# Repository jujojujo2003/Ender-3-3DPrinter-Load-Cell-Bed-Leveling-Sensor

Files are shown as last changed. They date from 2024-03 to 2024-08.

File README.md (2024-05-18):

# Ender-3-3DPrinter-Load-Cell-Bed-Leveling-Sensor
 This is a Load Cell based bed leveling sensor that should mount onto any vertical MGN12H gantry
 It uses
 * [ADS1235 ADC](https://www.digikey.com/en/products/detail/texas-instruments/ADS1235QWRHMRQ1/11308865) due to its 24-bit ADC, 7.2k sampling rate, 128x PGA gain.
 * [RP2040 MCU](https://www.raspberrypi.com/products/rp2040/) to do all the processing
 * [500g TAL 221 Loadcell](https://cdn.sparkfun.com/assets/9/9/a/f/3/TAL221.pdf) due to its compact nature. My gantry weighs around 250g. So make sure to select appropriate loadcell based on your gantry's weight so as to not saturate the loadcell.

My 3d printer is an Ender-3 with [3dFused's linear rail kit](https://3dfused.com/product/xaxis235/) and it perfectly works with that.

## PCB
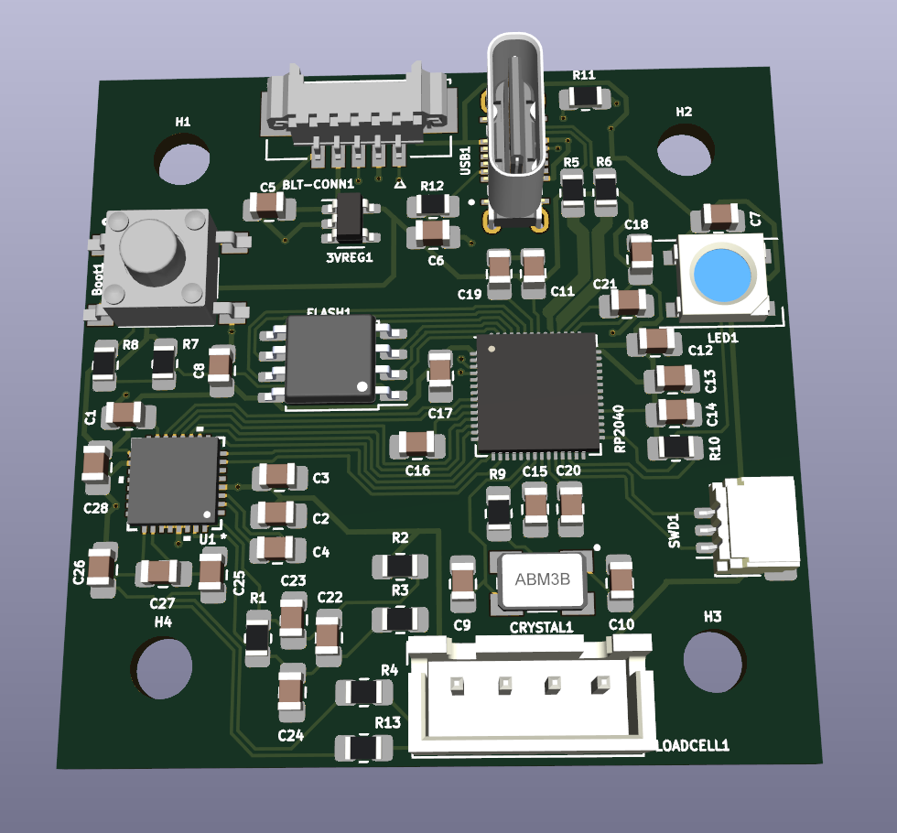
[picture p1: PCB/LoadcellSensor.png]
PCB Image


You can order this PCB on [OSHPark](https://oshpark.com/shared_projects/gbeaSpQu).
Alternatively, the KiCad Schematic is available on [github](https://github.com/jujojujo2003/MGN12H-3DPrinter-LoadCell-BedLevelingSensor/tree/main/PCB) and the [Digikey parts list here](https://github.com/jujojujo2003/MGN12H-3DPrinter-LoadCell-BedLevelingSensor/blob/main/PCB/LoadCellDigikeyParts.csv)

<TBD> Source code and mounting bracket

## Code

The Arduino IDE code is available [here](https://github.com/jujojujo2003/MGN12H-3DPrinter-LoadCell-BedLevelingSensor/tree/main/Code). 
* Install [Arduino IDE](https://www.arduino.cc/en/software)
* Install the following Arduino Libraries
  * [PioSPI](https://www.arduino.cc/reference/en/libraries/piospi/)
  * [Adafruit NeoPixel](https://www.arduino.cc/reference/en/libraries/adafruit-neopixel/)
  * [RunningAverage](https://www.arduino.cc/reference/en/libraries/runningaverage/)
* Try compiling the binary

Alternatively, you can flash the [precompiled binary](https://github.com/jujojujo2003/MGN12H-3DPrinter-LoadCell-BedLevelingSensor/releases/tag/release)

## Normal Operation
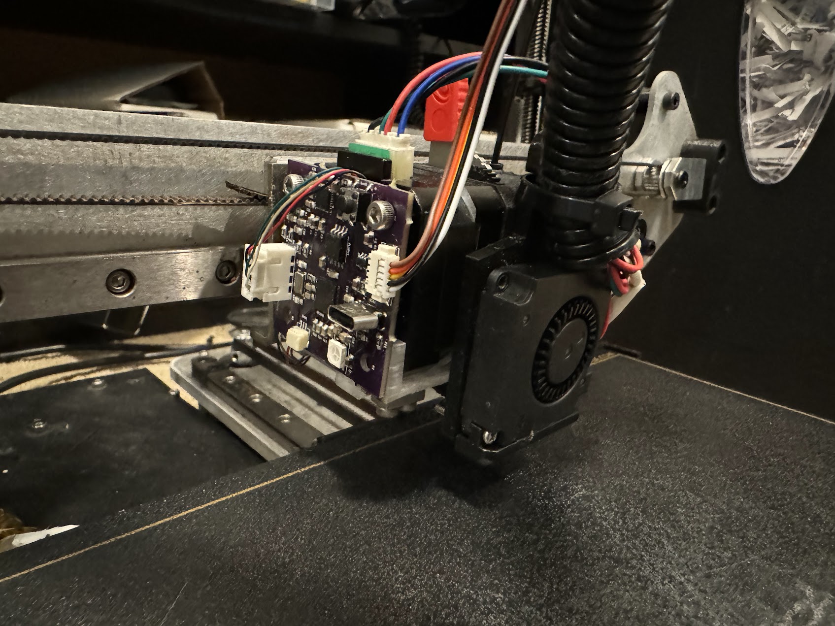
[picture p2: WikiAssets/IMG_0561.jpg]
Assembled Sensor


* If everything is wired correctly, as soon as you power on, the LED should be RED for a few seconds and then turn off. If it flashes red, then there is an error. Try connecting the USB port and check the debug message printed to serial. 

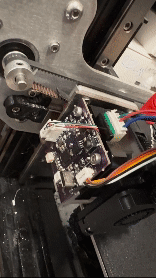
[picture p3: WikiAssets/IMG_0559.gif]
Initialization


* When the sensor is probing, the LED should turn blue to indicate that it is probing and turn green for a short while when triggered.

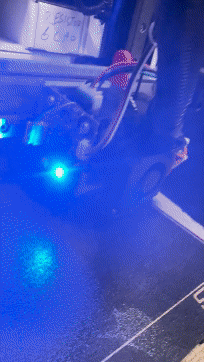
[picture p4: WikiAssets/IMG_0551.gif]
Triggered


## Tuning
[DELTA_FOR_TRIGGER](https://github.com/jujojujo2003/MGN12H-3DPrinter-LoadCell-BedLevelingSensor/blob/main/Code/bedlevelRp2040ADS1235.ino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) is the main tuning variable that controls the sensitivity of the probe.

* Typically, set DELTA_FOR_TRIGGER to a low value like 1-2 and set `is_probing = true`
* Reset your printer and as soon as it starts, the LED should be BLUE. Note that it might get triggers very easily and turn green since the threshold above is low.
* Keep the filament wire into the extruder tight and try to extrude filament or move the printer head and keep bumping up DELTA_FOR_TRIGGER till such motions don't trigger.
* Now the probe will only trigger for probing motions

## Z-Probe Repeatability Test
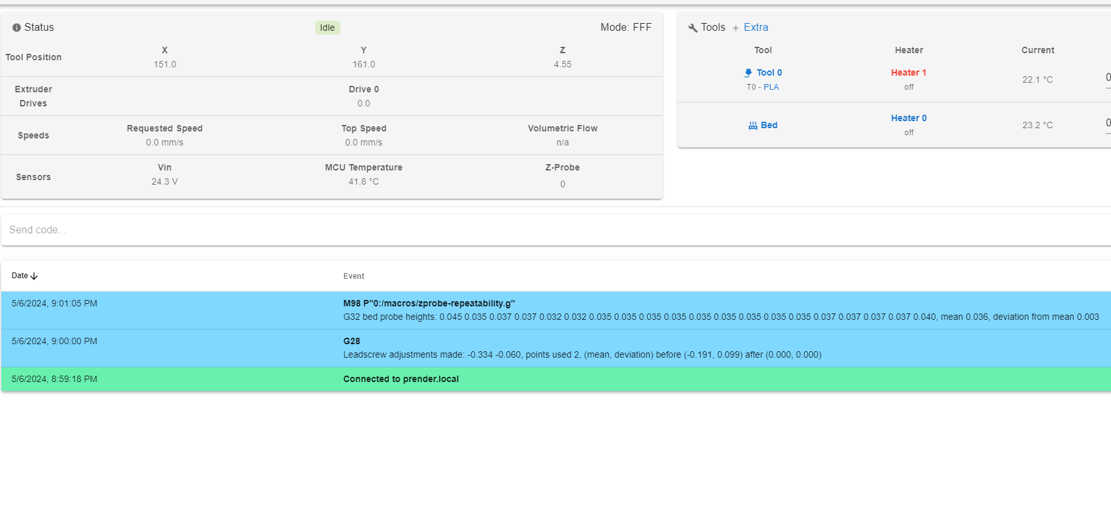
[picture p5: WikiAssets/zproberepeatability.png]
Z-Probe Repeatability Test


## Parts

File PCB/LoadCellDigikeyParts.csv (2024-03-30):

Reference | Value | Footprint | Datasheet | DigiKey_Part_Number | Qty
3VREG1 | AP2112K-3.3 | Package_TO_SOT_SMD:SOT-23-5 | https://www.diodes.com/assets/Datasheets/AP2112.pdf | AP2112K-3.3TRG1DICT-ND | 1
BLT-CONN1 | 532610571 | MolexPicoBlade:MOLEX_532610571 |  | WM7623CT-ND | 1
Boot1 | PTS645SK50SMTR92LFS | PushButton:SW_PTS645SK50SMTR92LFS |  | CKN9087TR-ND | 1
C1, C18, C21 | 1uF | Capacitor_SMD:C_0805_2012Metric_Pad1.18x1.45mm_HandSolder | ~ | 311-3498-1-ND | 3
C2 | 10uF | Capacitor_SMD:C_0805_2012Metric_Pad1.18x1.45mm_HandSolder | ~ | 399-C0805C106J8RACAUTO7210CT-ND | 1
C3, C8, C11-C17, C19, C20 | 0.1uF | Capacitor_SMD:C_0805_2012Metric_Pad1.18x1.45mm_HandSolder | ~ | 311-1858-1-ND | 11
C4 | 4.7nF | Capacitor_SMD:C_0805_2012Metric_Pad1.18x1.45mm_HandSolder | ~ | 399-C0805C472F5GEC7800CT-ND | 1
C5-C7 | 10uf | Capacitor_SMD:C_0805_2012Metric_Pad1.18x1.45mm_HandSolder | ~ | 399-C0805C106J8RACAUTO7210CT-ND | 3
C9, C10 | 12pF | Capacitor_SMD:C_0805_2012Metric_Pad1.18x1.45mm_HandSolder | ~ | 399-C0805C120C5GAC7800CT-ND | 2
C22, C27 | 10nF | Capacitor_SMD:C_0805_2012Metric_Pad1.18x1.45mm_HandSolder | ~ | 399-C0805C103J5GEC7800CT-ND | 2
C23-C26, C28 | 1nF | Capacitor_SMD:C_0805_2012Metric_Pad1.18x1.45mm_HandSolder | ~ | 399-17883-1-ND | 5
CRYSTAL1 | 12Mhz | ABM3B-12.000MHZ-12-N2Y-T:XTAL_ABM3B-12.000MHZ-12-N2Y-T |  | 535-14827-1-ND | 1
FLASH1 | W25Q128JVS | Package_SO:SOIC-8_5.23x5.23mm_P1.27mm | http://www.winbond.com/resource-files/w25q128jv_dtr%20revc%2003272018%20plus.pdf | W25Q128JVSIQCT-ND | 1
H1-H4 | MountingHole | MountingHole:MountingHole_3.5mm | ~ |  | 4
LED1 | WS2812B | LED_SMD:LED_WS2812B_PLCC4_5.0x5.0mm_P3.2mm | https://cdn-shop.adafruit.com/datasheets/WS2812B.pdf | WS2812B | 1
LOADCELL1 | B4B-XH-A | Connector_JST:JST_XH_B4B-XH-A_1x04_P2.50mm_Vertical |  |  | 1
R1 | 100k | Resistor_SMD:R_0805_2012Metric_Pad1.20x1.40mm_HandSolder | ~ | 13-RC0805FR-13100KLCT-ND | 1
R2-R4, R13 | 100 | Resistor_SMD:R_0805_2012Metric_Pad1.20x1.40mm_HandSolder | ~ | 311-100CRCT-ND | 4
R5, R6 | 27 | Resistor_SMD:R_0805_2012Metric_Pad1.20x1.40mm_HandSolder | ~ | 311-27.0CRCT-ND | 2
R7 | 10k | Resistor_SMD:R_0805_2012Metric_Pad1.20x1.40mm_HandSolder | ~ | 311-10.0KCRCT-ND | 1
R8, R9 | 1k | Resistor_SMD:R_0805_2012Metric_Pad1.20x1.40mm_HandSolder | ~ | 311-1.00KCRCT-ND | 2
R10 | 10K | Resistor_SMD:R_0805_2012Metric_Pad1.20x1.40mm_HandSolder | ~ | 311-10.0KCRCT-ND | 1
R11, R12 | 5.1k | Resistor_SMD:R_0805_2012Metric_Pad1.20x1.40mm_HandSolder | ~ | 311-5.10KCRCT-ND | 2
RP2040 | RP2040 | Package_DFN_QFN:QFN-56-1EP_7x7mm_P0.4mm_EP3.2x3.2mm | https://datasheets.raspberrypi.com/rp2040/rp2040-datasheet.pdf | 2648-SC0914(13)CT-ND | 1
SWD1 | ~ | Connector_JST:JST_SH_SM03B-SRSS-TB_1x03-1MP_P1.00mm_Horizontal | ~ | 455-SM03B-SRSS-TBCT-ND | 1
U1 | ADS1235IRHBR | ADS1235IRHBR:VQFN32_5X5_TEX |  | 296-ADS1235QWRHMRQ1CT-ND | 1
USB1 | ~ | USB4145-03-0170-C_REVA2:GCT_USB4145-03-0170-C_REVA2 |  | 2073-USB4145-03-0170-CCT-ND | 1

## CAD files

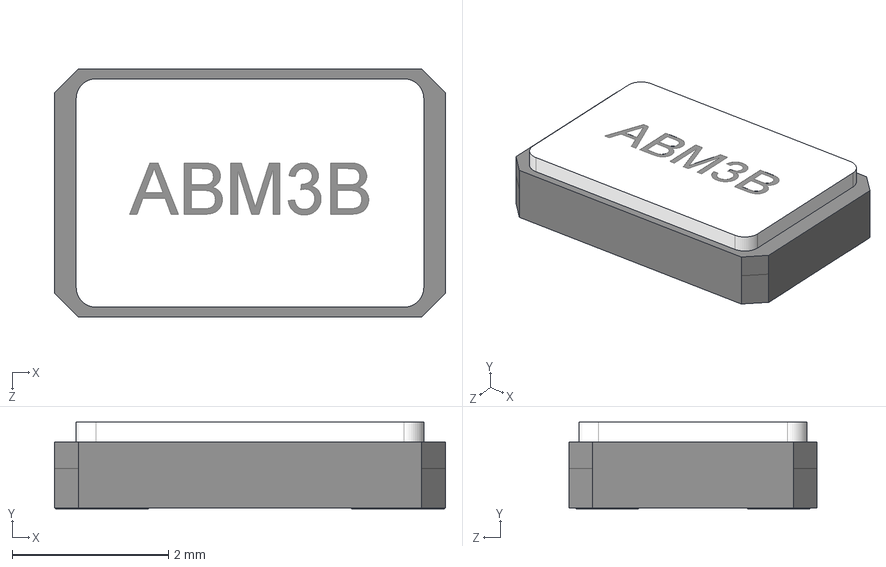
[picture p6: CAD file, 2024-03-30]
PCB/parts/ABM3B-12.000MHZ-12-N2Y-T/ABM3B-12.000MHZ-12-N2Y-T.step
5.00 x 1.11 x 3.18 mm

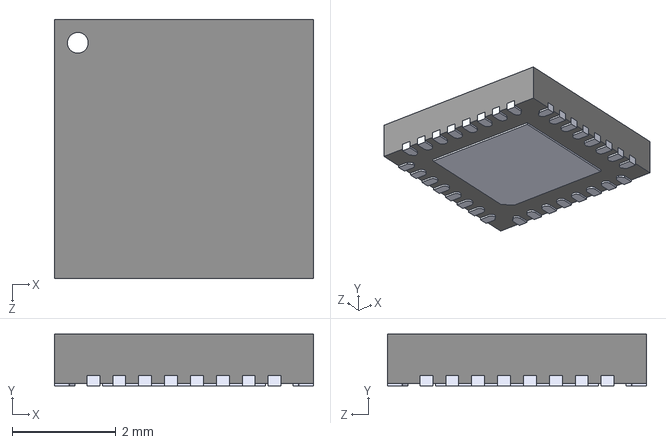
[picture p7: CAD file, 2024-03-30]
PCB/parts/ADS1235IRHBR/ADS1235IRHBR.step
5.00 x 1.00 x 5.00 mm

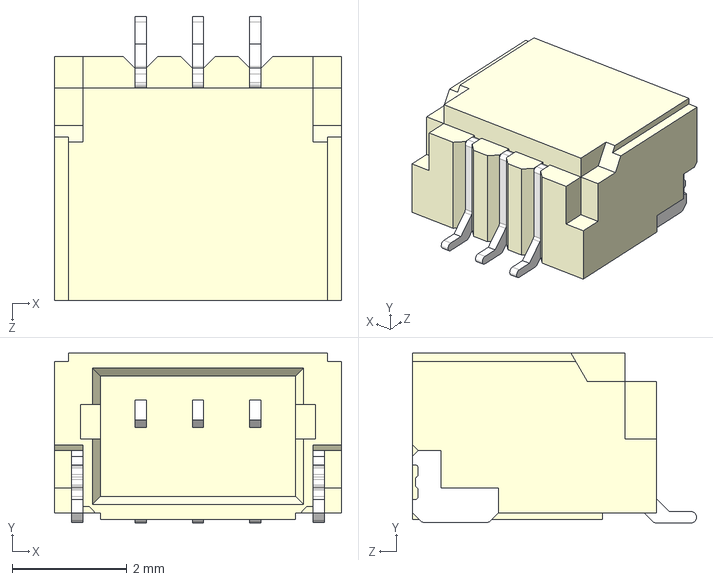
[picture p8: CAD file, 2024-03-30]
PCB/parts/jstsh/SM03B-SRSS-TB(LF)(SN)--3DModel-STEP-56544.STEP
5.00 x 2.96 x 4.95 mm

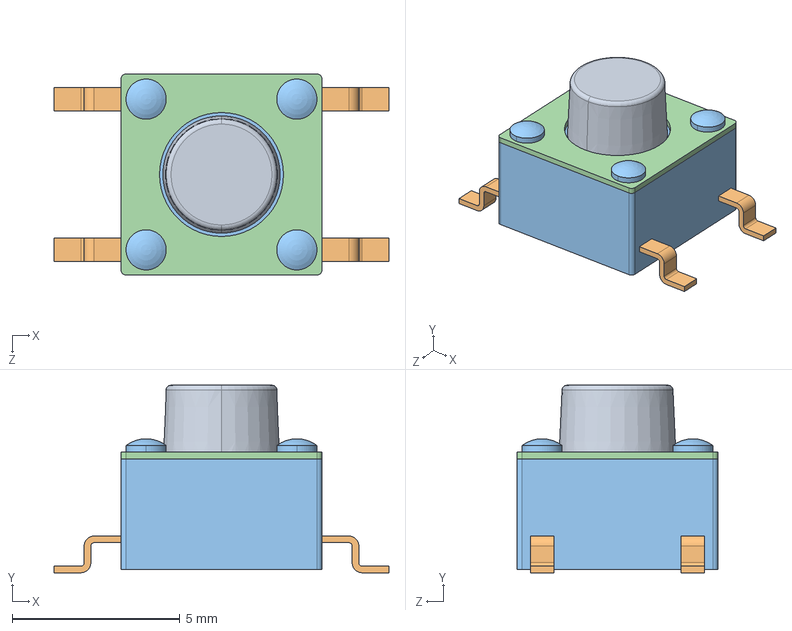
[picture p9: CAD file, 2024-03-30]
PCB/parts/PushButton/CUI_DEVICES_TS04-66-55-BK-160-SMT.step
10.0 x 5.60 x 6.00 mm

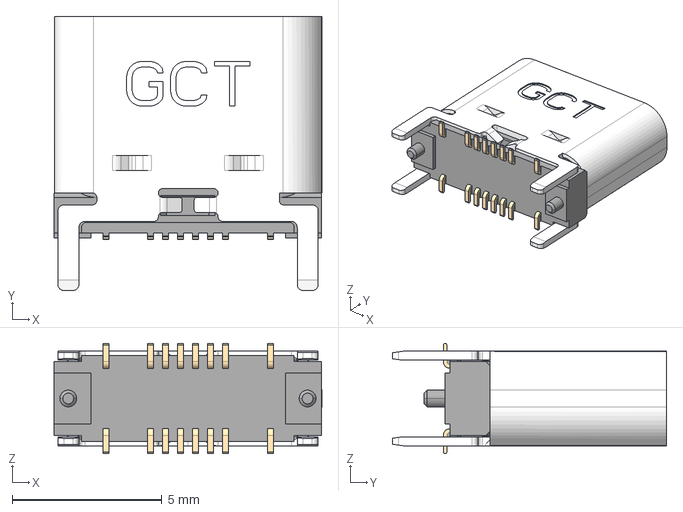
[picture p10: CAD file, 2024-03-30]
PCB/parts/USB4145-03-0170-C_REVA2/USB4145-03-0170-C_REVA2.step
8.95 x 9.16 x 3.69 mm

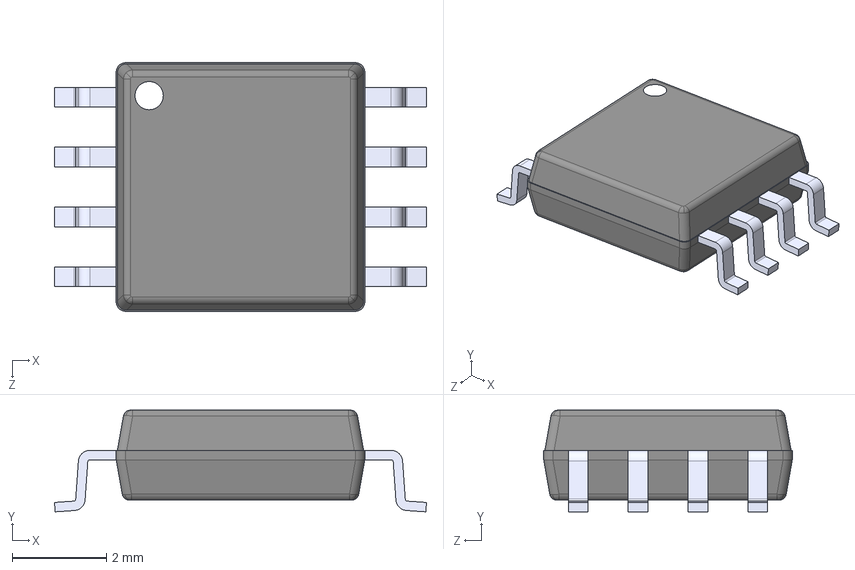
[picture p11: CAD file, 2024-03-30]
PCB/parts/W25Q128JVSIQ.STEP
7.90 x 2.16 x 5.28 mm

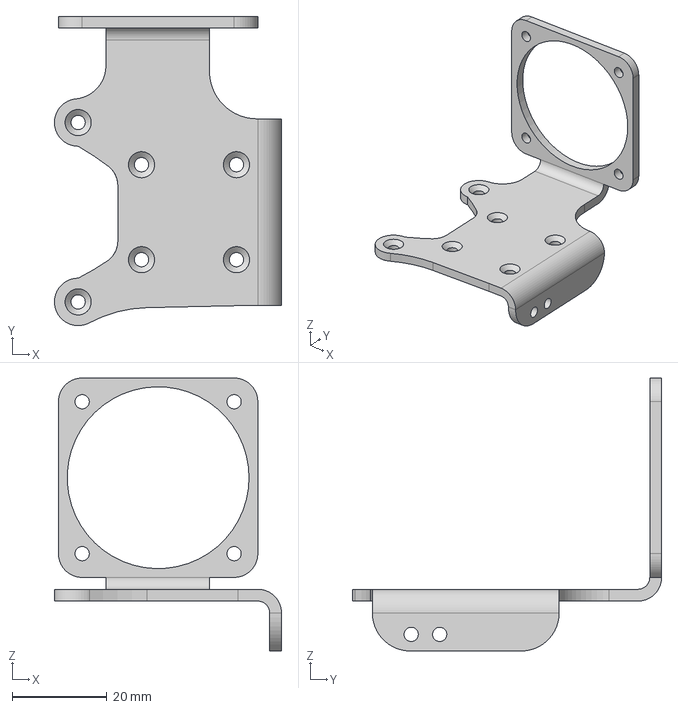
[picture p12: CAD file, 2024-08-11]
STL/MGN12H_LGX_ACE_Mount.step
47.8 x 65.1 x 57.5 mm

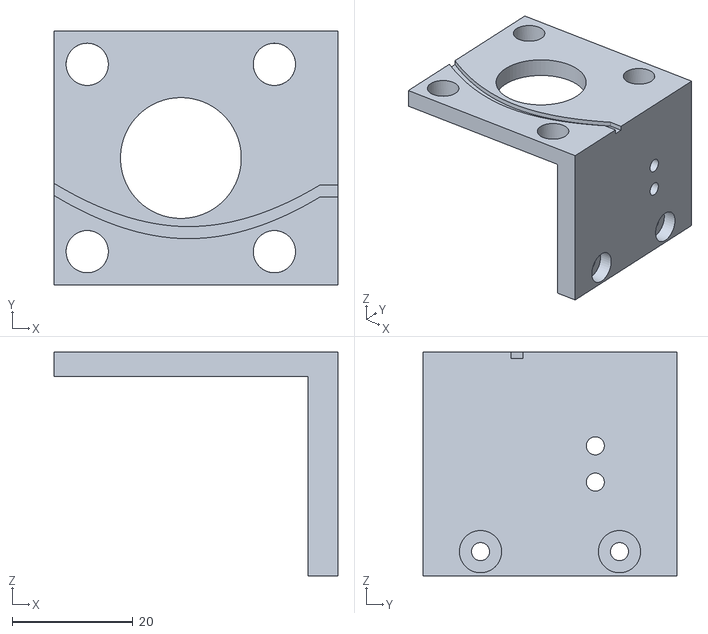
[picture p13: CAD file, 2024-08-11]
STL/TAL_221_LoadCell_mount.stl
47.0 x 42.0 x 37.0

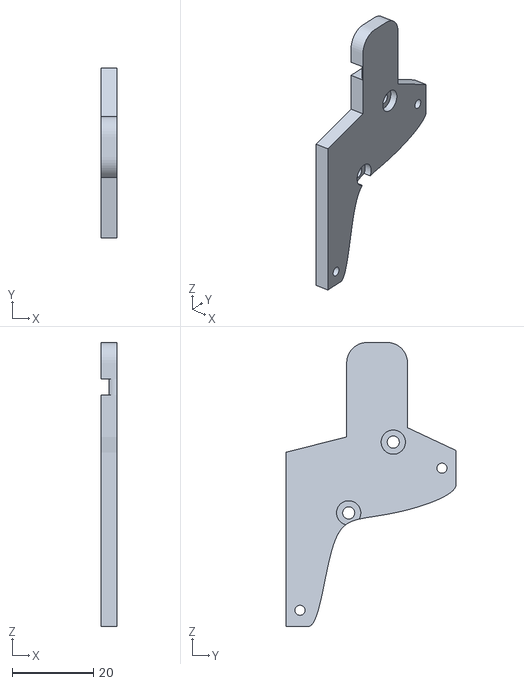
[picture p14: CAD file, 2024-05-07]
STL/4010_Fan_Mount.stl
4.00 x 42.0 x 70.0

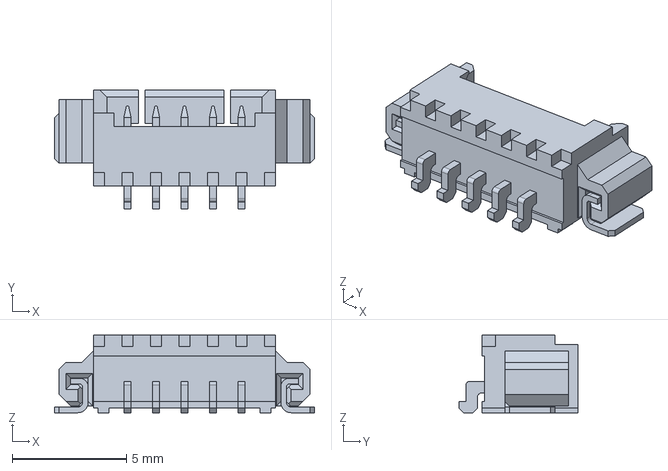
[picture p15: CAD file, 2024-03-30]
PCB/parts/MolexPicoBlade/532610571.step
11.4 x 5.20 x 3.40 mm

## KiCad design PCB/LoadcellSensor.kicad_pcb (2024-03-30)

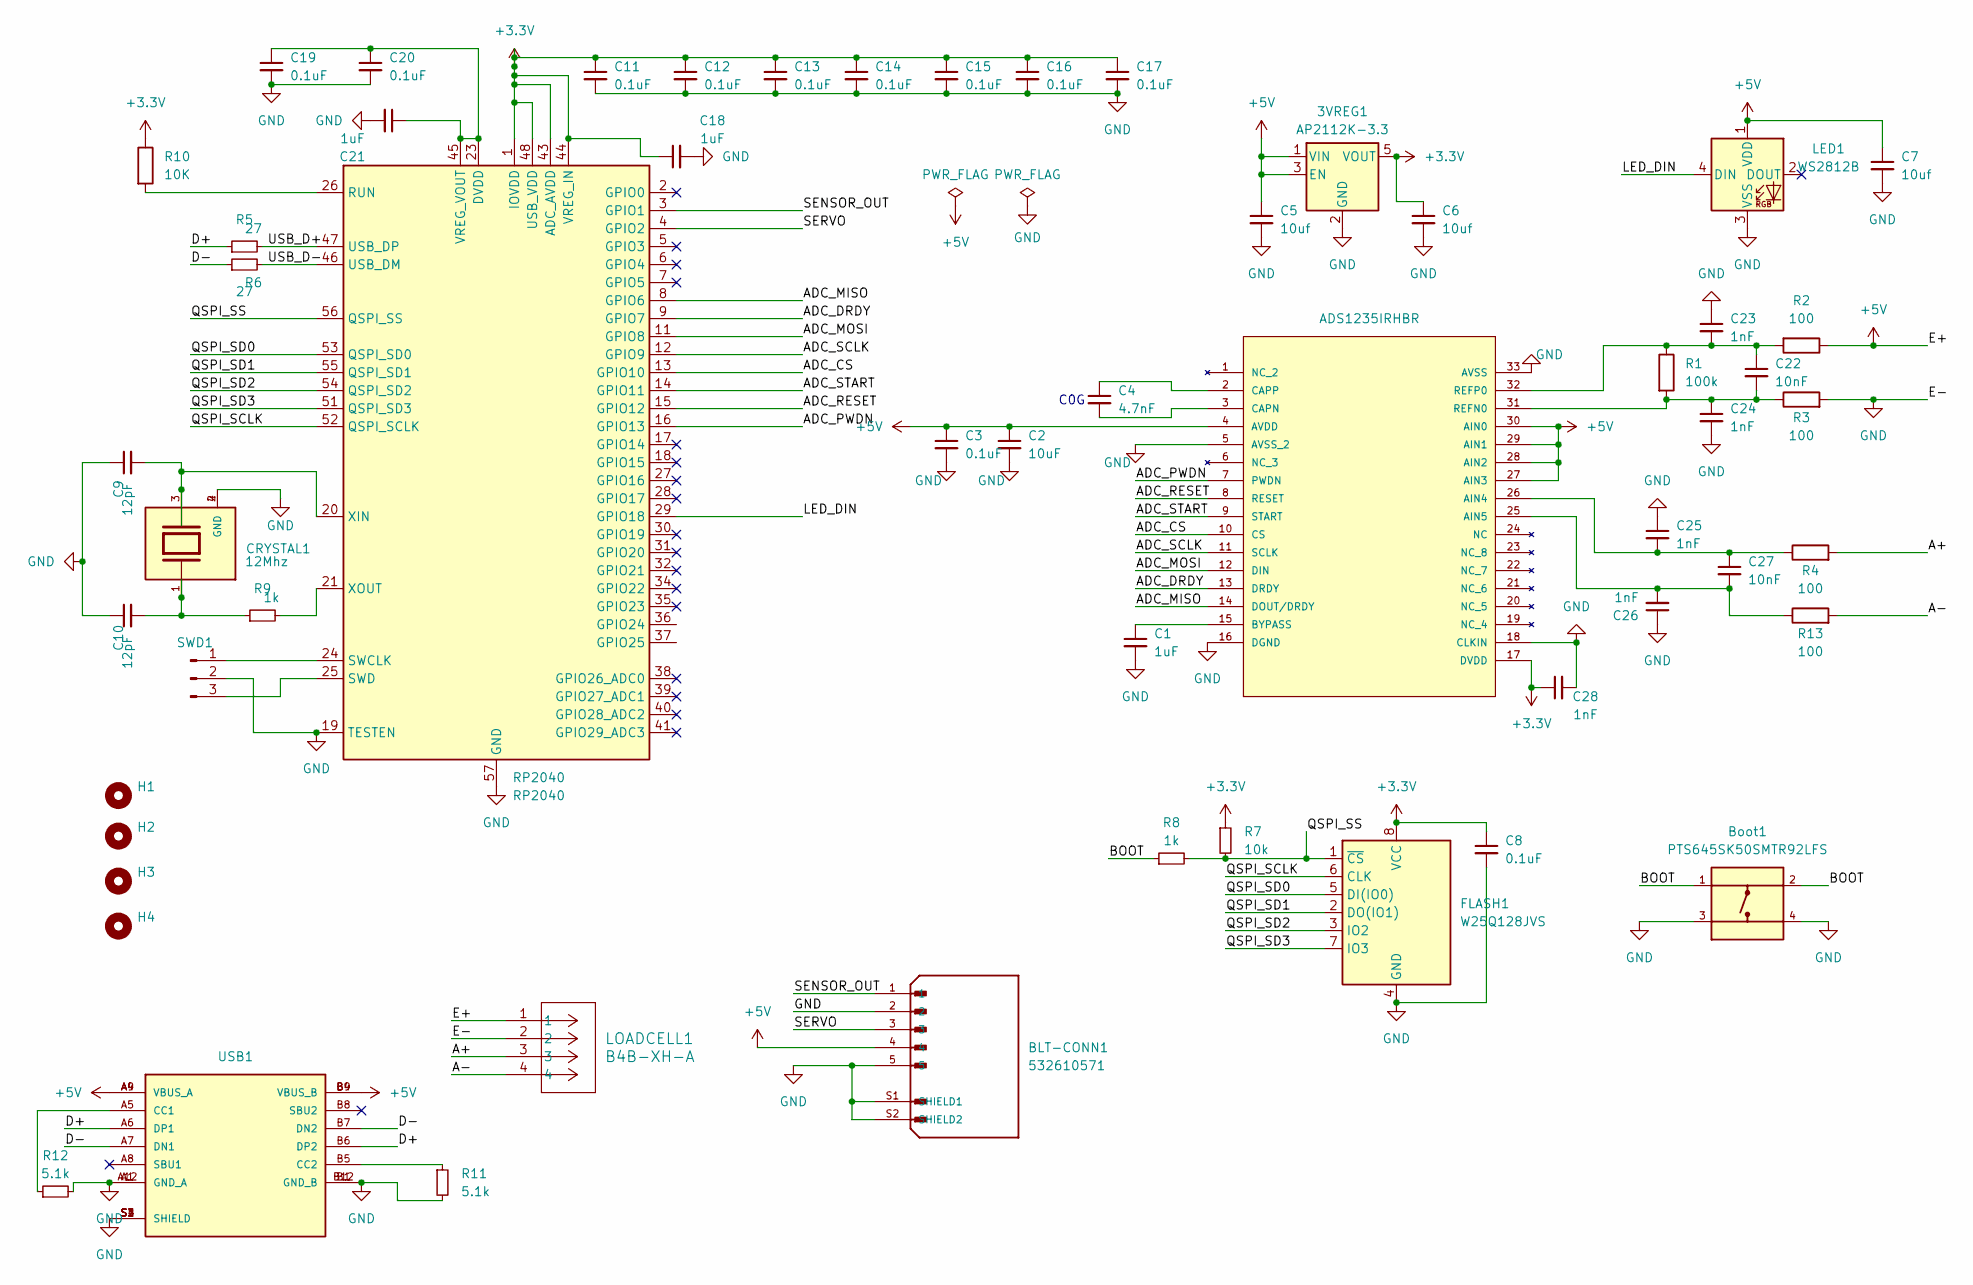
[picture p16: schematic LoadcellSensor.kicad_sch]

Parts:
3VREG1: AP2112K-3.3; SOT-23-5; DigiKey_Part_Number AP2112K-3.3TRG1DICT-ND
BLT-CONN1: 532610571; MOLEX_532610571; PARTREV J; DigiKey_Part_Number WM7623CT-ND
Boot1: PTS645SK50SMTR92LFS; SW_PTS645SK50SMTR92LFS; DigiKey_Part_Number CKN9087TR-ND
C1, C18, C21: 1uF; C_0805_2012Metric_Pad1.18x1.45mm_HandSolder; DigiKey_Part_Number 311-3498-1-ND
C2: 10uF; C_0805_2012Metric_Pad1.18x1.45mm_HandSolder; DigiKey_Part_Number 399-C0805C106J8RACAUTO7210CT-ND
C3, C8, C11, C12, C13, C14, C15, C16, C17, C19, C20: 0.1uF; C_0805_2012Metric_Pad1.18x1.45mm_HandSolder; DigiKey_Part_Number 311-1858-1-ND
C4: 4.7nF; C_0805_2012Metric_Pad1.18x1.45mm_HandSolder; DigiKey_Part_Number 399-C0805C472F5GEC7800CT-ND
C5, C6, C7: 10uf; C_0805_2012Metric_Pad1.18x1.45mm_HandSolder; DigiKey_Part_Number 399-C0805C106J8RACAUTO7210CT-ND
C9, C10: 12pF; C_0805_2012Metric_Pad1.18x1.45mm_HandSolder; DigiKey_Part_Number 399-C0805C120C5GAC7800CT-ND
C22, C27: 10nF; C_0805_2012Metric_Pad1.18x1.45mm_HandSolder; DigiKey_Part_Number 399-C0805C103J5GEC7800CT-ND
C23, C24, C25, C26, C28: 1nF; C_0805_2012Metric_Pad1.18x1.45mm_HandSolder; DigiKey_Part_Number 399-17883-1-ND
CRYSTAL1: 12Mhz; XTAL_ABM3B-12.000MHZ-12-N2Y-T; PARTREV 08.25.15; DigiKey_Part_Number 535-14827-1-ND
FLASH1: W25Q128JVS; SOIC-8_5.23x5.23mm_P1.27mm; DigiKey_Part_Number W25Q128JVSIQCT-ND
H1, H2, H3, H4: MountingHole; MountingHole_3.5mm
LED1: WS2812B; LED_WS2812B_PLCC4_5.0x5.0mm_P3.2mm; DigiKey_Part_Number WS2812B
LOADCELL1: B4B-XH-A; JST_XH_B4B-XH-A_1x04_P2.50mm_Vertical
R1: 100k; R_0805_2012Metric_Pad1.20x1.40mm_HandSolder; DigiKey_Part_Number 13-RC0805FR-13100KLCT-ND
R2, R3, R4, R13: 100; R_0805_2012Metric_Pad1.20x1.40mm_HandSolder; DigiKey_Part_Number 311-100CRCT-ND
R5, R6: 27; R_0805_2012Metric_Pad1.20x1.40mm_HandSolder; DigiKey_Part_Number 311-27.0CRCT-ND
R7: 10k; R_0805_2012Metric_Pad1.20x1.40mm_HandSolder; DigiKey_Part_Number 311-10.0KCRCT-ND
R8, R9: 1k; R_0805_2012Metric_Pad1.20x1.40mm_HandSolder; DigiKey_Part_Number 311-1.00KCRCT-ND
R10: 10K; R_0805_2012Metric_Pad1.20x1.40mm_HandSolder; DigiKey_Part_Number 311-10.0KCRCT-ND
R11, R12: 5.1k; R_0805_2012Metric_Pad1.20x1.40mm_HandSolder; DigiKey_Part_Number 311-5.10KCRCT-ND
RP2040: RP2040; QFN-56-1EP_7x7mm_P0.4mm_EP3.2x3.2mm; DigiKey_Part_Number 2648-SC0914(13)CT-ND
SWD1: JST_SH_SM03B-SRSS-TB_1x03-1MP_P1.00mm_Horizontal; DigiKey_Part_Number 455-SM03B-SRSS-TBCT-ND
U1: ADS1235IRHBR; VQFN32_5X5_TEX; MANUFACTURER_PART_NUMBER ADS1235IRHBR; DigiKey_Part_Number 296-ADS1235QWRHMRQ1CT-ND
USB1: GCT_USB4145-03-0170-C_REVA2; PARTREV A2; DigiKey_Part_Number 2073-USB4145-03-0170-CCT-ND

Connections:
+3.3V: 3VREG1.5 (VOUT), C6.1, C8.1, C11.1, C12.1, C13.1, C14.1, C15.1, C16.1, C17.1, C18.1, C28.1, FLASH1.8 (VCC), R7.1, R10.1, RP2040.1 (IOVDD), RP2040.10 (IOVDD), RP2040.22 (IOVDD), RP2040.33 (IOVDD), RP2040.42 (IOVDD), RP2040.43 (ADC_AVDD), RP2040.44 (VREG_IN), RP2040.48 (USB_VDD), RP2040.49 (IOVDD), U1.17 (DVDD)
+5V: 3VREG1.1 (VIN), 3VREG1.3 (EN), BLT-CONN1.4, C2.1, C3.1, C5.1, C7.1, LED1.1 (VDD), LOADCELL1.1, R2.1, U1.4 (AVDD), U1.27 (AIN3), U1.28 (AIN2), U1.29 (AIN1), U1.30 (AIN0), USB1.A4 (VBUS_A), USB1.A9 (VBUS_A), USB1.B4 (VBUS_B), USB1.B9 (VBUS_B)
/A+: LOADCELL1.3, R4.2
/A-: LOADCELL1.4, R13.2
/ADC_CS: RP2040.13 (GPIO10), U1.10 (CS)
/ADC_DRDY: RP2040.9 (GPIO7), U1.13 (DRDY)
/ADC_MISO: RP2040.8 (GPIO6), U1.14 (DOUT/DRDY)
/ADC_MOSI: RP2040.11 (GPIO8), U1.12 (DIN)
/ADC_PWDN: RP2040.16 (GPIO13), U1.7 (PWDN)
/ADC_RESET: RP2040.15 (GPIO12), U1.8 (RESET)
/ADC_SCLK: RP2040.12 (GPIO9), U1.11 (SCLK)
/ADC_START: RP2040.14 (GPIO11), U1.9 (START)
/BOOT: Boot1.1, Boot1.2, R8.1
/D+: R5.1, USB1.A6 (DP1), USB1.B6 (DP2)
/D-: R6.1, USB1.A7 (DN1), USB1.B7 (DN2)
/LED_DIN: LED1.4 (DIN), RP2040.29 (GPIO18)
/QSPI_SCLK: FLASH1.6 (CLK), RP2040.52 (QSPI_SCLK)
/QSPI_SD0: FLASH1.5 (DI(IO0)), RP2040.53 (QSPI_SD0)
/QSPI_SD1: FLASH1.2 (DO(IO1)), RP2040.55 (QSPI_SD1)
/QSPI_SD2: FLASH1.3 (IO2), RP2040.54 (QSPI_SD2)
/QSPI_SD3: FLASH1.7 (IO3), RP2040.51 (QSPI_SD3)
/QSPI_SS: FLASH1.1 (~CS), R7.2, R8.2, RP2040.56 (QSPI_SS)
/SENSOR_OUT: BLT-CONN1.1, RP2040.3 (GPIO1)
/SERVO: BLT-CONN1.3, RP2040.4 (GPIO2)
/USB_D+: R5.2, RP2040.47 (USB_DP)
/USB_D-: R6.2, RP2040.46 (USB_DM)
GND: 3VREG1.2 (GND), BLT-CONN1.2, BLT-CONN1.5, BLT-CONN1.S1 (SHIELD1), BLT-CONN1.S2 (SHIELD2), Boot1.3, Boot1.4, C1.2, C2.2, C3.2, C5.2, C6.2, C7.2, C8.2, C9.1, C10.1, C11.2, C12.2, C13.2, C14.2, C15.2, C16.2, C17.2, C18.2, C19.2, C20.2, C21.2, C23.1, C24.2, C25.1, C26.1, C28.2, CRYSTAL1.2 (GND), CRYSTAL1.4 (GND), FLASH1.4 (GND), LED1.3 (VSS), LOADCELL1.2, R3.2, R11.2, R12.2, RP2040.19 (TESTEN), RP2040.57 (GND), SWD1.2, U1.5 (AVSS_2), U1.16 (DGND), U1.18 (CLKIN), U1.33 (AVSS), USB1.A1 (GND_A), USB1.A12 (GND_A), USB1.B1 (GND_B), USB1.B12 (GND_B), USB1.S1 (SHIELD), USB1.S2 (SHIELD), USB1.S3 (SHIELD), USB1.S4 (SHIELD)
unnamed: C10.2, CRYSTAL1.1, R9.1
unnamed: R10.2, RP2040.26 (RUN)
unnamed: RP2040.24 (SWCLK), SWD1.1
unnamed: RP2040.25 (SWD), SWD1.3
unnamed: C19.1, C20.1, C21.1, RP2040.23 (DVDD), RP2040.45 (VREG_VOUT), RP2040.50 (DVDD)
unnamed: C9.2, CRYSTAL1.3, RP2040.20 (XIN)
unnamed: R9.2, RP2040.21 (XOUT)
unnamed: C25.2, C27.1, R4.1, U1.26 (AIN4)
unnamed: C26.2, C27.2, R13.1, U1.25 (AIN5)
unnamed: C1.1, U1.15 (BYPASS)
unnamed: C4.2, U1.3 (CAPN)
unnamed: C4.1, U1.2 (CAPP)
unnamed: C22.2, C24.1, R1.2, R3.1, U1.31 (REFN0)
unnamed: C22.1, C23.2, R1.1, R2.2, U1.32 (REFP0)
unnamed: R12.1, USB1.A5 (CC1)
unnamed: R11.1, USB1.B5 (CC2)

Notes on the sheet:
C0G

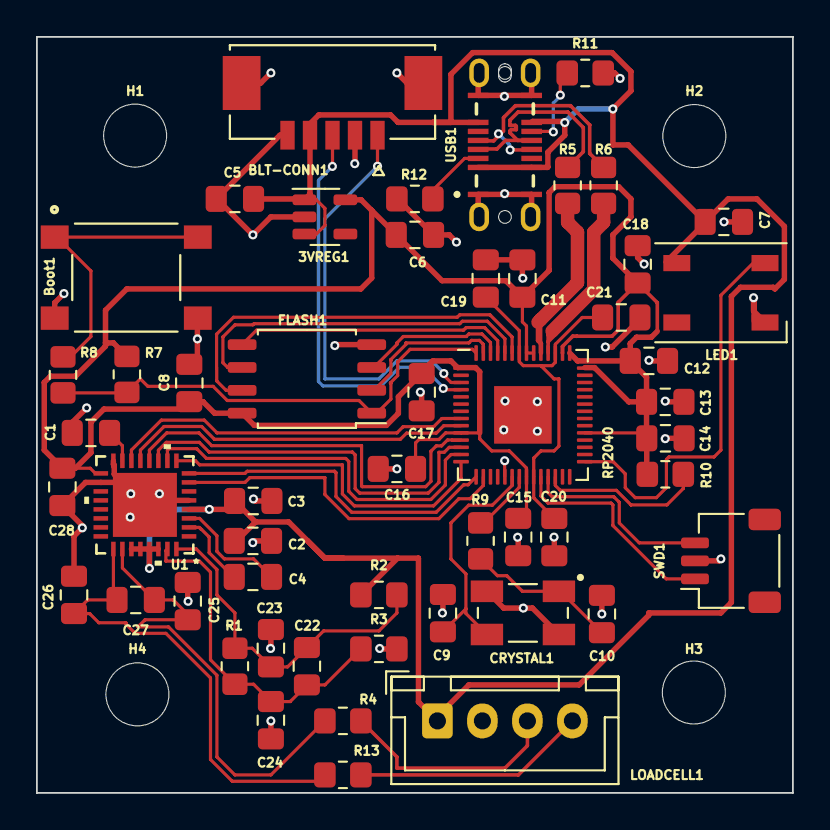
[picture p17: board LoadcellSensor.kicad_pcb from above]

Board: 2 copper layers, 42.0 x 42.0 mm, 56 parts (0 on the bottom side), 43 nets.

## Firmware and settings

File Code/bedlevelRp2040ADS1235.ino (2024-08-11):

#include <SPI.h>
#include "PioSPI.h"
#include "ADS1235.h"
#include <Adafruit_NeoPixel.h>

//==================Config Variables========================
// Percentage of deviation allowed before probe trigger signal is sent
#define DELTA_FOR_TRIGGER 5

// Required target accuracy in mm for sensor
#define TARGET_ACCURACY 0.001 

// Probing speed in mm/min
#define PROBING_SPEED 30

// Number of samples to read to check if stable value is achieved
#define SAMPLES_FOR_STABILIZATION 10

// Relative percentage value before sample deemed stable. Value of one means wait for all samples to be ±1%
#define TOLERANCE_FOR_STABILIZATION 0.5

// How many ms to wait before fetching next sample
#define STABILIZATION_SAMPLING_INTERVAL_IN_MS 100

// ADS sampling speed
#define ADS_SPEED ADS1235::DataRate::SPS_7200

//===========================END============================

// ADC Pins
#define ADC_MISO 6
#define ADC_NOT_DRDY 7
#define ADC_MOSI 8
#define ADC_SCLK 9
#define ADC_CS 10
#define ADC_START 11
#define ADC_NOT_RESET 12
#define ADC_NOT_PWDN 13

// MCU PINS
#define LED_DIN 18
#define CONTROL_PIN 2
#define OUTPUT_PIN 1

PioSPI spiBus(ADC_MOSI, ADC_MISO, ADC_SCLK, ADC_CS, SPI_MODE1, 20000000);
SPISettings spiSettings(20000000, MSBFIRST, SPI_MODE1);
Adafruit_NeoPixel led(1, LED_DIN, NEO_GRB + NEO_KHZ800);

// State variables
uint64_t ledEndTime = 0;
uint32_t ledColor = 0;
bool is_probing = false;
unsigned long interruptRisingEdgeTime = 0;
uint16_t numberOfSamplesForProbing = 1; 

void halt(String reason) {
  unsigned long int start = millis();
  while ((millis()-start)<=2000) {
    if (micros() % 1000 == 0) {
      Serial.print("Halted: ");
      Serial.println(reason);
    }
    if ((millis() / 100) % 2 == 0) {
      led.fill(led.Color(255, 0, 0));
    } else {
      led.fill(led.Color(0, 0, 0));
    }
    led.show();
  }

  ADS1235::getInstance()->reset();
  NVIC_SystemReset();
}

void handleControlPinChange() {
  if (is_probing) {
    // If already probing, don't accept any more command
    return;
  }
  int input = digitalRead(CONTROL_PIN);
  if (input == HIGH) {
    interruptRisingEdgeTime = micros();
  } else {
    unsigned long int delta = micros() - interruptRisingEdgeTime;
    interruptRisingEdgeTime = 0;
    // BLTouch
    // https://youprintin3d.de/media/pdf/54/75/b4/f5a1c8_77037f55e5d542309d9fc178165c9f3f.pdf
    // Pin Down dutycycle 650us ±20 as per spec
    if (delta >= 620 && delta <= 680) {
      is_probing = true;
    }
  }
}

void updateLED() {
  if (is_probing) {
    led.fill(led.Color(0, 0, 255));
    led.show();
  } else if (ledEndTime == 0) {
    // Nothing to  do
  } else if (millis() < ledEndTime) {
    // Show color
    led.fill(ledColor);
    led.show();
  } else {
    // Clear LED reset state
    ledEndTime = 0;
    led.clear();
    led.show();
  }
}

void setLEDAndClearAfter(uint64_t duration_millis, uint32_t color) {
  ledEndTime = millis() + duration_millis;
  ledColor = color;
  updateLED();
}

void trigger() {
  digitalWrite(OUTPUT_PIN, HIGH);
  setLEDAndClearAfter(1000, led.Color(0, 255, 0));
  Serial.println("Triggered");
  delay(10);
  digitalWrite(OUTPUT_PIN, LOW);
}

double getNormalizedReadingFromADC() {
  return ADS1235::getInstance()->getRunningAverage()->getAverageLast(numberOfSamplesForProbing) * 100.0 / ADS1235::getInstance()->getRunningAverage()->getAverage();
}

void setup() {
  Serial.begin(115200);
  Serial.println("Inititalizing");
  
  pinMode(OUTPUT_PIN, OUTPUT);
  digitalWrite(OUTPUT_PIN, LOW);
  pinMode(CONTROL_PIN, INPUT_PULLUP);

  led.fill(led.Color(0, 0, 0));
  led.show();

  spiBus.begin();
  ADS1235::createInstance(spiBus, spiSettings, ADC_NOT_RESET, ADC_NOT_PWDN, ADC_START, ADC_NOT_DRDY);
  ADS1235::getInstance()->init();
  ADS1235::getInstance()->setInputMux(ADS1235::InputMux::AIN4, ADS1235::InputMux::AIN5);
  ADS1235::getInstance()->setDataRate(ADS_SPEED);
  ADS1235::getInstance()->setMode(ADS1235::ADCMode::NORMAL);
  ADS1235::getInstance()->caliberate();

  led.fill(led.Color(255, 0, 0));
  led.show();
  // Wait for buffer to fill
  while(!ADS1235::getInstance()->getRunningAverage()->bufferIsFull());
  led.fill(led.Color(255, 80, 0));
  led.show();

  // Verify settings
  if (ADS1235::getInstance()->getDataRate() != ADS_SPEED) {
    halt("Incorrect Datarate!");
  }

  if (ADS1235::getInstance()->getPositiveInputMux() != ADS1235::InputMux::AIN4) {
    halt("Incorrect Positive mux!");
  }

  if (ADS1235::getInstance()->getNegativeInputMux() != ADS1235::InputMux::AIN5) {
    halt("Incorrect Negative mux!");
  }

  if (ADS1235::getInstance()->getMode() != ADS1235::ADCMode::NORMAL) {
    halt("Incorrect MODE!");
  }

  // Make real time sampling data rate is roughtly same as what we set on initialization
  double dataRateRatio = (ADS1235::getInstance()->getRealDataRateAsInt()*1.0/ADS1235::getInstance()->getDataRateAsInt());
  if (dataRateRatio > 1.1 || dataRateRatio < 0.9) {
    halt("Realtime data rate not the same as what was set. Please check ADC connections");
  }

  // Samples to average for probing is number of samples that can fit in the time probe takes to travel TARGET_ACCURACY distance with PROBING_SPEED
  numberOfSamplesForProbing = ceil(ADS1235::getInstance()->getRealDataRateAsInt()*(TARGET_ACCURACY/(PROBING_SPEED/60.0)));
  if (numberOfSamplesForProbing < 1) {
    halt("numberOfSamplesForProbing < 1 . Your sensor is not capable of hitting the target accuracy given the probing speed. Try changing either of them");
  }

  // Setup Interupts
  attachInterrupt(CONTROL_PIN, handleControlPinChange, CHANGE);

  // Wait for data to stabilize
  // Fetch data at 100 ms intervals and wait for all 10 sample points to be ± 1 of avg value 
  double data[SAMPLES_FOR_STABILIZATION];
  uint8_t last_ptr = 0;
  while(last_ptr<SAMPLES_FOR_STABILIZATION){
    data[last_ptr] = getNormalizedReadingFromADC();
    delay(STABILIZATION_SAMPLING_INTERVAL_IN_MS);
    last_ptr++;
  }
  bool has_stabilized = true;
  do {
    has_stabilized = true;
    for(int i=0;i<SAMPLES_FOR_STABILIZATION;i++) {
      if (data[i] > (100+TOLERANCE_FOR_STABILIZATION) || data[i] < (100-TOLERANCE_FOR_STABILIZATION)) {
        // Data not stable
        has_stabilized = false;
        // get next value
        last_ptr = (last_ptr+1)%SAMPLES_FOR_STABILIZATION;
        data[last_ptr]  = getNormalizedReadingFromADC();
        led.fill(led.Color(255*((millis()/100)%2), 80*((millis()/100)%2), 0));
        led.show();
        delay(STABILIZATION_SAMPLING_INTERVAL_IN_MS);
        break;
      }
    }
  } while(!has_stabilized);
  led.fill(led.Color(0, 255, 0));
  led.show();
  delay(1000);
  led.fill(led.Color(0, 0, 0));
  led.show();
}

void loop() {
  updateLED();
  // Uncomment for debug logs
  /*if (micros()%100000 ==0) {
    Serial.print(ADS1235::getInstance()->getRealDataRateAsInt());
    Serial.print(" ");
    Serial.print(numberOfSamplesForProbing);
    Serial.print(" ");
    Serial.print(getNormalizedReadingFromADC());
    Serial.println();
  }*/
  if (is_probing) {
    double normalizedValue = getNormalizedReadingFromADC();
    if (normalizedValue <= (100 - DELTA_FOR_TRIGGER) || normalizedValue >= (100 + DELTA_FOR_TRIGGER)) {
      // Probing  done
      // Reset state variables
      is_probing = false;
      trigger();
    }
  }
}

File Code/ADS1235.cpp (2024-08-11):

#include "ADS1235.h"

ADS1235* ADS1235::singleton = nullptr;

ADS1235::ADS1235(SPIClass& spi_, SPISettings& spi_settings, uint8_t nrst_pin, uint8_t npwdn_pin, uint8_t start_pin, uint8_t ndrdy_pin) {
  this->spi = &spi_;
  this->spiSettings = &spi_settings;
  this->nrstPin = nrst_pin;
  this->npwdnPin = npwdn_pin;
  this->startPin = start_pin;
  this->ndrdyPin = ndrdy_pin;
}

void ADS1235::init() {
  pinMode(this->nrstPin, OUTPUT);
  digitalWrite(this->nrstPin, HIGH);

  pinMode(this->npwdnPin, OUTPUT);
  digitalWrite(this->npwdnPin, HIGH);

  pinMode(this->startPin, OUTPUT);
  digitalWrite(this->startPin, HIGH);

  pinMode(this->ndrdyPin, INPUT_PULLUP);
  delay(100);
  this->reset();
  attachInterrupt(this->ndrdyPin, this->handleDrdyChange, FALLING);
}

void ADS1235::reset() {
  digitalWrite(this->startPin, LOW);
  delay(100);
  digitalWrite(this->startPin, HIGH);
}

void ADS1235::exchangeData(unsigned char* data, unsigned char* rx_buffer, size_t size) {
  this->spi->beginTransaction(*this->spiSettings);
  this->spi->transfer(data, rx_buffer, size);
  this->spi->endTransaction();
}

uint8_t ADS1235::readRegister(Register reg) {
  unsigned char data[3] = { 0 }, rx_buffer[3] = { 0 };
  data[0] = (uint8_t)reg + 0x20;
  this->exchangeData(data, rx_buffer, sizeof(data));
  return rx_buffer[2];
}

void ADS1235::writeRegister(Register reg, unsigned char payload) {
  digitalWrite(this->startPin, LOW);
  unsigned char data[2] = { 0 }, rx_buffer[2] = { 0 };
  data[0] = 0x40 + (uint8_t)reg;
  data[1] = payload;
  this->exchangeData(data, rx_buffer, sizeof(data));
  digitalWrite(this->startPin, HIGH);
}

void ADS1235::setMode(ADCMode mode){
  uint8_t reg = this->readRegister(ADS1235::Register::MODE1);
  reg = (reg & 0b10011111) | (mode << 5);
  this->writeRegister(ADS1235::Register::MODE1, reg);   
}

ADS1235::ADCMode ADS1235::getMode(){
  uint8_t reg = this->readRegister(ADS1235::Register::MODE1);
  uint8_t mode = (reg & 0b01100000) >> 5;
  return static_cast<ADCMode>(mode);
}

void ADS1235::caliberate() {
  unsigned char data[2] = { 0 }, rx_buffer[2] = { 0 };
  data[0] = 0x19;
  this->exchangeData(data, rx_buffer, sizeof(data));
  delay(500);

  // Measure number of samples we get in 1 sec in real time
  this->calibrationStartMicros = micros();
  this->numberOfSamplesPerSec = 0;

  // Wait for enough interrupts on handleDrdyChange
  while((micros() - this->calibrationStartMicros) < SECONDS_IN_MICROS);

  if (this->runningAverage != NULL) {
    delete this->runningAverage;
  }
  this->runningAverage = new RunningAverage(this->numberOfSamplesPerSec*2);
  this->runningAverage->clear();
}

void ADS1235::setInputMux(InputMux positive, InputMux negative) {
  uint8_t payload = ((uint8_t)positive << 4) | ((uint8_t)negative);
  this->writeRegister(Register::INPMUX, payload);
}

ADS1235::InputMux ADS1235::getInputMuxFromByte(uint8_t byte) {
  switch (byte) {
    case InputMux::AIN0: 
      return InputMux::AIN0;
    case InputMux::AIN1: 
      return InputMux::AIN1;
    case InputMux::AIN2: 
      return InputMux::AIN2;
    case InputMux::AIN3: 
      return InputMux::AIN3;
    case InputMux::AIN4: 
      return InputMux::AIN4;
    case InputMux::AIN5: 
      return InputMux::AIN5;
  }
  return InputMux::INVALID_MUX;
}

ADS1235::InputMux ADS1235::getPositiveInputMux() {
  uint8_t reg = this->readRegister(ADS1235::Register::INPMUX);
  return getInputMuxFromByte((reg >> 4) & 0b00001111);
}

ADS1235::InputMux ADS1235::getNegativeInputMux() {
  uint8_t reg = this->readRegister(ADS1235::Register::INPMUX);
  return getInputMuxFromByte((reg) & 0b00001111);
}

void ADS1235::setDataRate(DataRate rate) {
  uint8_t reg = this->readRegister(Register::MODE0);
  reg = (reg & 0b10000111) | (rate << 3);
  this->writeRegister(Register::MODE0, reg);
}

ADS1235::DataRate ADS1235::getDataRate() {
  uint8_t reg = this->readRegister(Register::MODE0);
  reg = (reg >> 3) & 0b00001111;
  switch (reg) {
    case DataRate::SPS_2:
      return DataRate::SPS_2;
    case DataRate::SPS_5:
      return DataRate::SPS_5;
    case DataRate::SPS_10:
      return DataRate::SPS_10;
    case DataRate::SPS_16:
      return DataRate::SPS_16;
    case DataRate::SPS_20:
      return DataRate::SPS_20;
    case DataRate::SPS_50:
      return DataRate::SPS_50;
    case DataRate::SPS_60:
      return DataRate::SPS_60;
    case DataRate::SPS_100:
      return DataRate::SPS_100;
    case DataRate::SPS_400:
      return DataRate::SPS_400;
    case DataRate::SPS_1200:
      return DataRate::SPS_1200;
    case DataRate::SPS_2400:
      return DataRate::SPS_2400;
    case DataRate::SPS_4800:
      return DataRate::SPS_4800;
    case DataRate::SPS_7200:
      return DataRate::SPS_7200;
  }

  return DataRate::INVALID_DR; 
}

int ADS1235::getDataRateAsInt() {
  uint8_t reg = this->readRegister(Register::MODE0);
  reg = (reg >> 3) & 0b00001111;
  switch (reg) {
    case DataRate::SPS_2:
      return 2;
    case DataRate::SPS_5:
      return 5;
    case DataRate::SPS_10:
      return 10;
    case DataRate::SPS_16:
      return 16;
    case DataRate::SPS_20:
      return 20;
    case DataRate::SPS_50:
      return 50;
    case DataRate::SPS_60:
      return 60;
    case DataRate::SPS_100:
      return 100;
    case DataRate::SPS_400:
      return 400;
    case DataRate::SPS_1200:
      return 1200;
    case DataRate::SPS_2400:
      return 2400;
    case DataRate::SPS_4800:
      return 4800;
    case DataRate::SPS_7200:
      return 7200;
  }

  return -1; 
}

int ADS1235::getRealDataRateAsInt() {
  return this->numberOfSamplesPerSec;
}

long ADS1235::readADCRaw() {
  unsigned char data[6] = { 0 }, rx_buffer[6] = { 0 };
  data[0] = 0x12;
  this->exchangeData(data, rx_buffer, sizeof(data));
  bool isNegative = (bool)((rx_buffer[2] & 0b10000000) >> 7);
  int32_t value =(((uint32_t)(isNegative ? 0xFF : 0x00)) << 24) + (((uint32_t)rx_buffer[2]) << 16) + (((uint32_t)rx_buffer[3]) << 8) + ((uint32_t)rx_buffer[4]);
  return value;
}

ADS1235* ADS1235::getInstance() {
  return singleton;
}
void ADS1235::createInstance(SPIClass& spi_, SPISettings& spi_settings, uint8_t nrst_pin, uint8_t npwdn_pin, uint8_t start_pin, uint8_t ndrdy_pin) {
  if (ADS1235::singleton != NULL) {
    return;
  }
  ADS1235::singleton = new ADS1235(
    spi_,
    spi_settings,
    nrst_pin,
    npwdn_pin,
    start_pin,
    ndrdy_pin
  );
}

void ADS1235::maybeUpdateNumberOfSamplesPerSec() {
  if ((micros() - this->calibrationStartMicros) < SECONDS_IN_MICROS) {
    this->numberOfSamplesPerSec++;
  }
}

RunningAverage* ADS1235::getRunningAverage() {
  return this->runningAverage;
}

void ADS1235::handleDrdyChange() {
  ADS1235::getInstance()->maybeUpdateNumberOfSamplesPerSec();
  if (ADS1235::getInstance()->getRunningAverage() != NULL) {
    long val = ADS1235::getInstance()->readADCRaw();
    ADS1235::getInstance()->getRunningAverage()->addValue(val);
  }
}

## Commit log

2024-03-30 PCB commit
    [532610571.step, ABM3B-12.000MHZ-12-N2Y-T.step, ADS1235IRHBR.step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]
2024-05-07 Add STL
    [4010_Fan_Mount.stl, TAL_221_LoadCell_mount.stl]
2024-08-11 Add averaging for probing as well
    [MGN12H_LGX_ACE_Mount.step, TAL_221_LoadCell_mount.stl]

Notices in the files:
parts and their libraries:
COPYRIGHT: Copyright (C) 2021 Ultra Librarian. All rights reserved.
